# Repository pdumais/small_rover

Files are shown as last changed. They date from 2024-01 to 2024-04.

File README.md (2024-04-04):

# A remote controlled vehicle with a mechanical arm using ESP32 and a PS5 Dualsense controller
It's heavy, it's noisy, it's klonky and it looks like a rudimentary machine. That's exactly what I wanted to build.
This is work in progress, so no pictures of the final build yet

Rover (https://youtu.be/MDsiWHeAhvQ)
Rover (https://youtu.be/R3Qs6OE4Az8)

# Electronics
I chose to use 2 ESP32. It would have been easier to use just one, but I needed the memory of a esp32-s3 and the classic BT from the ESP32. So I'm using both. 
The ESP32 is the DualSense (PS5 controller) receiver. It handles the connection and incoming data from the Dualsense
and sends it on the i2c bus. This device will most probably end up handling other misc stuff too.

The esp32-s3 is main controller.
    - Controls the 4 motors
    - Controls servo for steering
    - Reads pulse count for each motors (RPM reading)
    - Controls the buzzer
    - Controls LED ring
  
# Choice of motors
I'm using 4 12v DC motors with a stall current of 7A with 4 DRV8871 that limits current to 2A for each motor.
The PWM signal to control the motor is shared for all DRV8871 so 4WD is disabled by software. Emiting the PWM on 3 more pins 
and requiring the motors would enable 4WD.

I tried to do the maths for calculating how big of a motor I would need to make something from steel, so targeting 5kgs.
Every number I came with gave me way too big requirements for motor size. This didn't make any sense considering the current offer of motors. So I decided to aim 251RPM and get high torque. 50$ a motor sounded like expensive so I guess it's good.
It turns out the torque is sufficient since the drv8871 doesn't seem to suffer. But 251RPM is faster than what I need. I would half that if I have to buy new motors.

After shopping around, it seems like building something that requires more than 10A of total current draw would be a different game. Different manufacturer and different tutorials. This hinted me that I should stick to this limit.

# PS5 Controller
I found an ESP32 ps5 library at https://github.com/rodneybakiskan/ps5-esp32.git but it was made for Arduino and is not maintained.
So I modified it to make it work outside the Arduino environment with only ESP-IDF. I'm having problems with it though. 
Connecting the controller is a hit or miss, sometimes I have to reboot the board and retry many times. But it works fine when 
using the Arduino version. I suspect it has something to do with multithreading/multicore since there seems to be a race condition when the controller tries to connect to the board and the board tries to connect to the controller at the same time. So I disabled the connection attempt from the board and it now works. I'll have to make a better fix later.

The controller is a bluetooth device so it has a range limit of 10m, but that's not an issue since I only plan on using this in the house.

# Frame
I chose to use steel for the frame. Aluminum would be better, but I don't have the tools to work aluminum. Plus, aluminum is expensive.
I developed an interest in welding lately so I wanted to play around with my tools.

## Motor mounts
The motor mounting brackets were a bit of a challenge for me. I used a piece of paper and poke holes where the screw holes of them motor were. Then I glued the the paper on a sheet of metal and cut/drilled it.

Of course the first piece I built was bad, but the second one only has 1 hole misaligned. Close enough.
So I now use that piece as a template to build more.

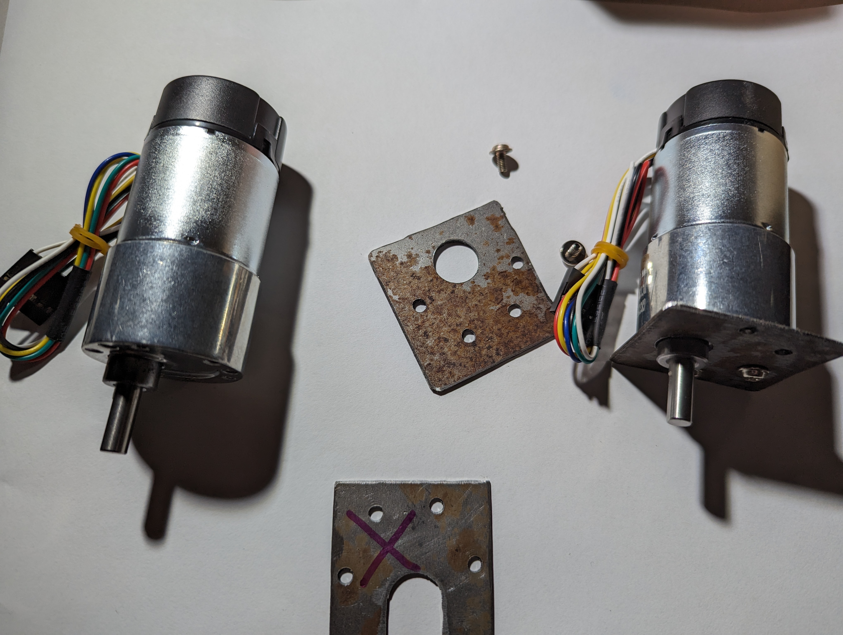
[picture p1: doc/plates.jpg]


## Subframe
The subframe is just a 3cm wide steel bar welded on the rear axle and bolted on the from one. I prefered to put bolts on the front s o it would be easier to put a better steering mechanism in place some time.

The vehicle is separated in 4 sections: The steering, battery mount, main board and mechanical arm.
There is a series of holes on the subframe that allows me to bolt the battery mount and main board at varying distances.

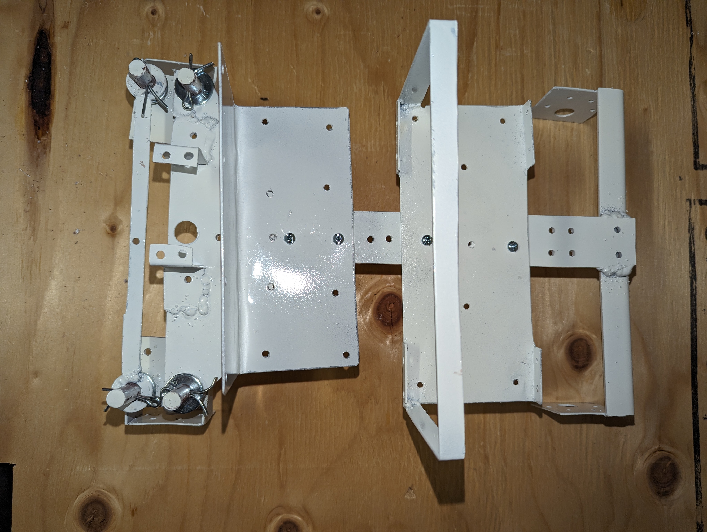
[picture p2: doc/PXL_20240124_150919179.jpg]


# Steering
To build a steering, I practiced a few prototypes with Legos. Then I ended up building something like this:
It's not perfect, but it works. Using ball joints would be much better.
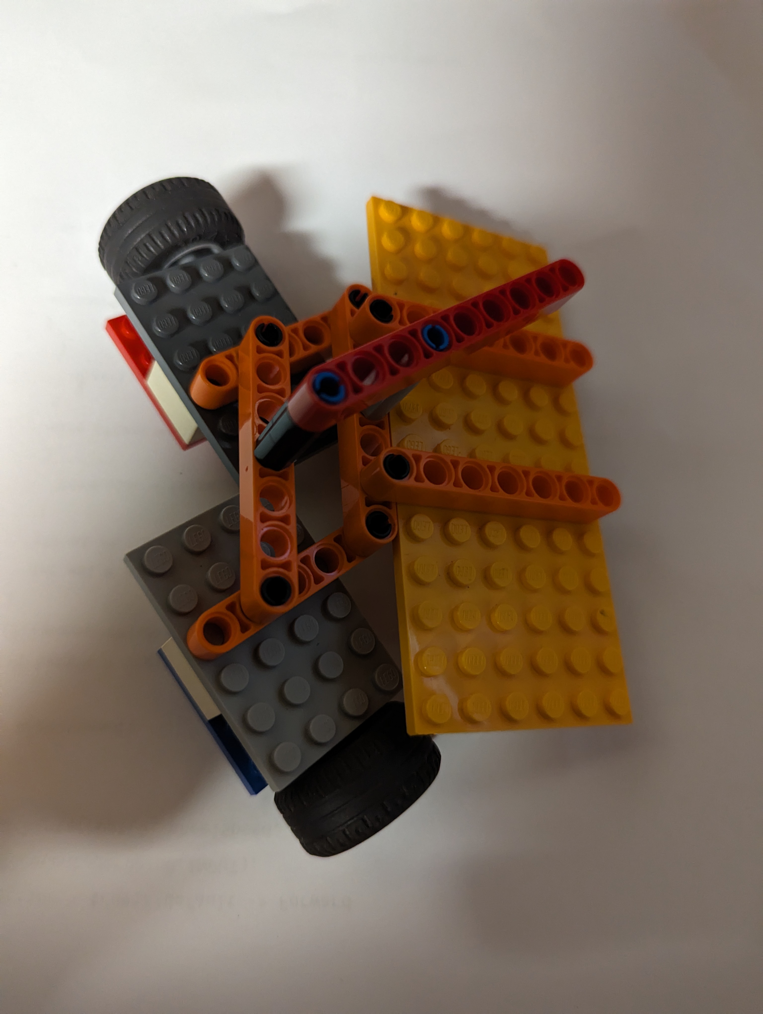
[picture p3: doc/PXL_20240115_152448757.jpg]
<p style="text-align: center;"> 
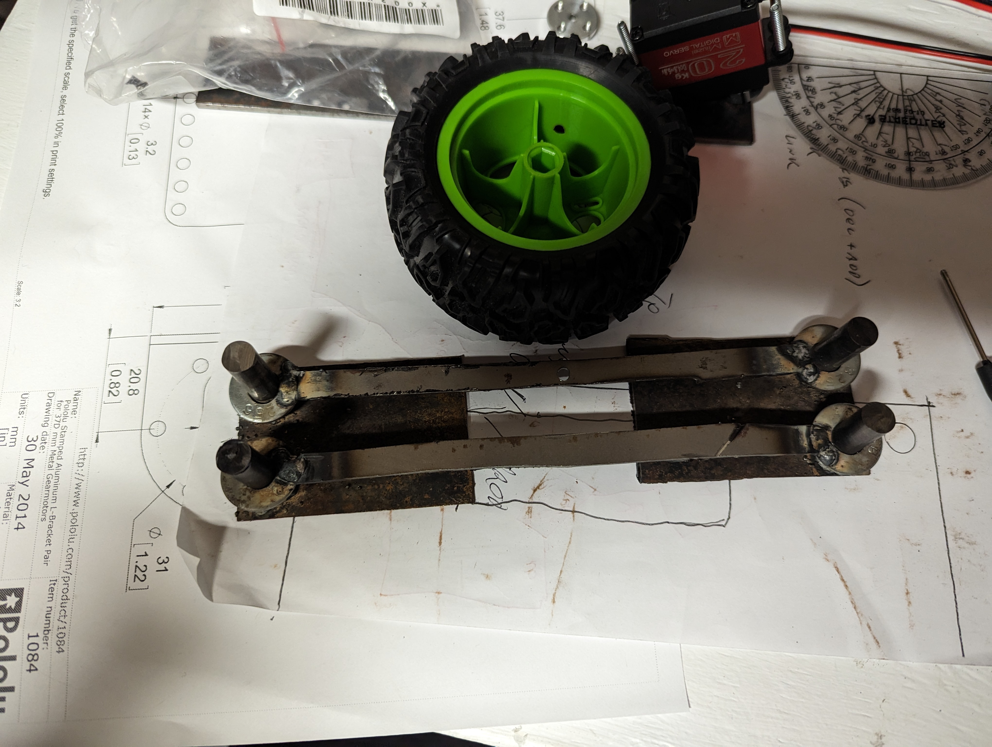
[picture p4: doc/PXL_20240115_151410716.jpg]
</p>

# Battery mount
The battery mount is just an L-shape plate on which the battery is tie-wrapped.
The battery sits on a foam to reduce vibrations.

# Main board
The main board is a piece of plywood on which all PCBs are screwed. It consists of the main ESP32 board, the PS5 controller ESP32 board and 2 small 5v regulators.

** Update march 1st.
I created a PCB design to make things a bit more cleaner. I dit not receive the board from the fab yet, but I'm planning on replacing the protoboard with this one

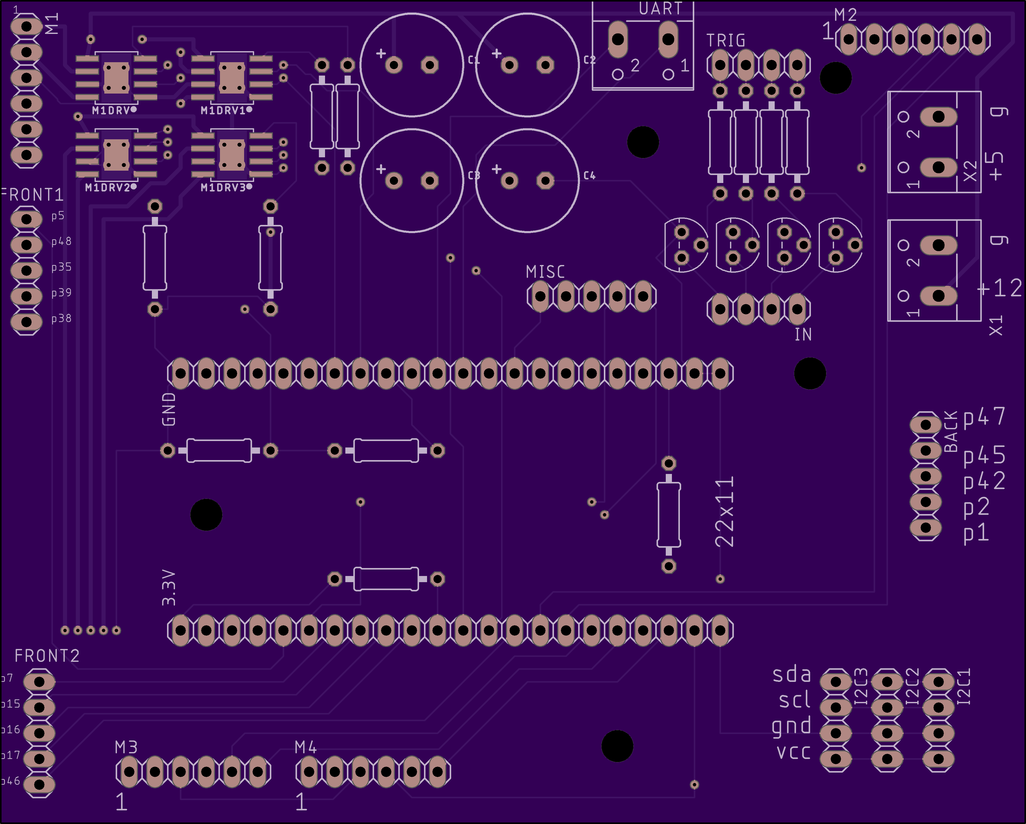
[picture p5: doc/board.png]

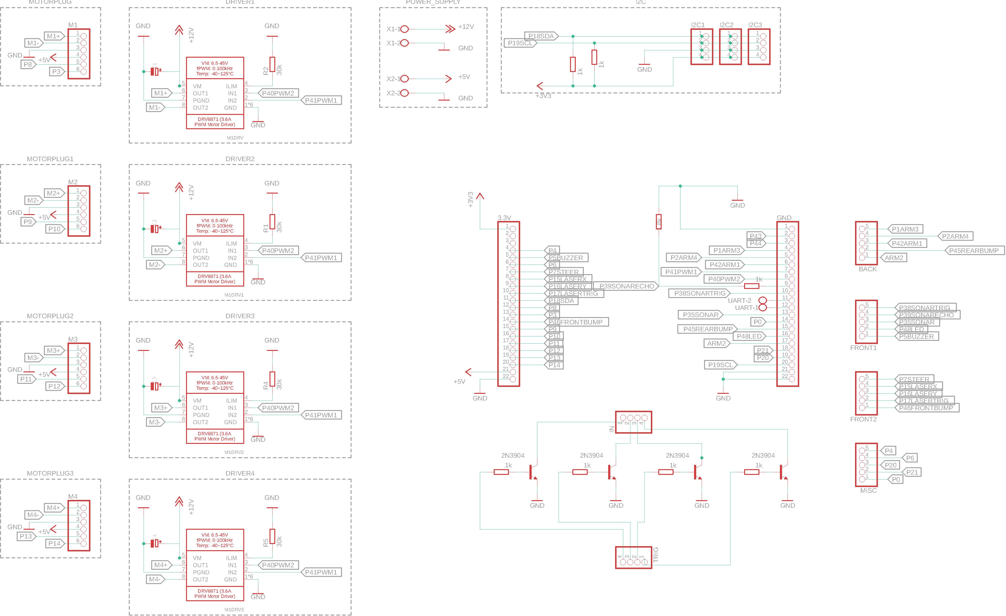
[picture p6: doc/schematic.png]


** Update April 2nd.

I finally got the board mounted on the robot.  As with all boards I make, there are a few design flaws on this one. But nothing that can't be fixed. The first issue is that I didn't think about the fact the motors on the right side would need to turn the opposite way from the ones on the left side. So I should've reverse the ouput lines comming from the motor driver for those. The fix was to simply reverse the pins on the motor connectors.

The 2nd flaw is that the 3 signal lines going to the servos for the laser and the sonar are running right above the motor output lines. So when I start the motors, it creates noise on the signal lines and the servos are going crazy. The fix for this was to add a 1k resistor inline on the signal cables. I'm not sure if that's the right fix, but it does work. It's nice to see how the noise being introduced is proportional to the current being used by the motors. For example, noise only happens what starting the motors or stopping them. I understand how electromagnectic induction works, but I didn't think it would be this sensitive.
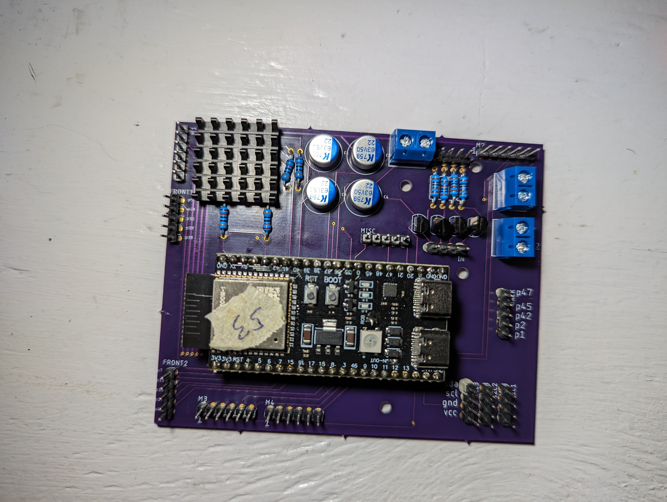
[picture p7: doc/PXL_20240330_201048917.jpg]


# Mechanical Arm
The goal was to be able to lift a 500ml can of beer.

- Base
    - Sits on bearing. Base is a big gear but not 360. Like the chute of a snoblower
    - regular DC motor with gear to spin the base. 
        - No need for high torque. No need for high speed although the gear ratio of the base must be taken in consideration

- Boom and Arm
    - 2 regular motors. Or servos? Servos cant be controlled like a real bakhoe
    - Sitting on the base. Pulling the boom and arm using levers
- Grapple
    - Servo sitting on the arm

I wanted the feel of the arm to be like a backhoe control. My initial implementation was taking a value from the Dualsense constroller sticks. This value is between -128 and 127 and was mapped to an angle on the betwwen 0 and 90 on the servo.
This has the affect of using the controller to bring the arm to a set value instead of simply accellerating the arm, like a hydraulic system would. This is a big difference in feel. Also, when releasing the DualSense stick, the servo would return back to its original position. In a hydraulic system, you simply want the arm to stop moving and stay at its current position.

It took a fair amount of code to replicate this behaviour but I'm overall satisfied. It definitely feels more "mechanic" that fluid like a hydraulic system but I think I like it.

The arm can only be used while in "arm" mode. Arm mode is activated/deactivated with the Dualsense cross button.
While in arm mode, the throttle is disabled and the steering is disable to be able to use the sticks for controlling the arm.
Another reason, is that it would require too much power to run the 4 motors and the servos at the same time.
To reduce power usage event more, only 1 servo per sticks can be used at the same time. The 5v regulator that feeds the servo cannot exceed 3A.

# Telemetry
The machine creates a WAP and has the IP address 192.168.4.1. It sends telemetry data over a websocket every second. This packet
contains the metrics of the machine as defined in [mainboard/main/common.h](mainboard//main/common.h) in `struct metrics_t`. There is web page served on port 80 to render the raw data into a user friendly view.
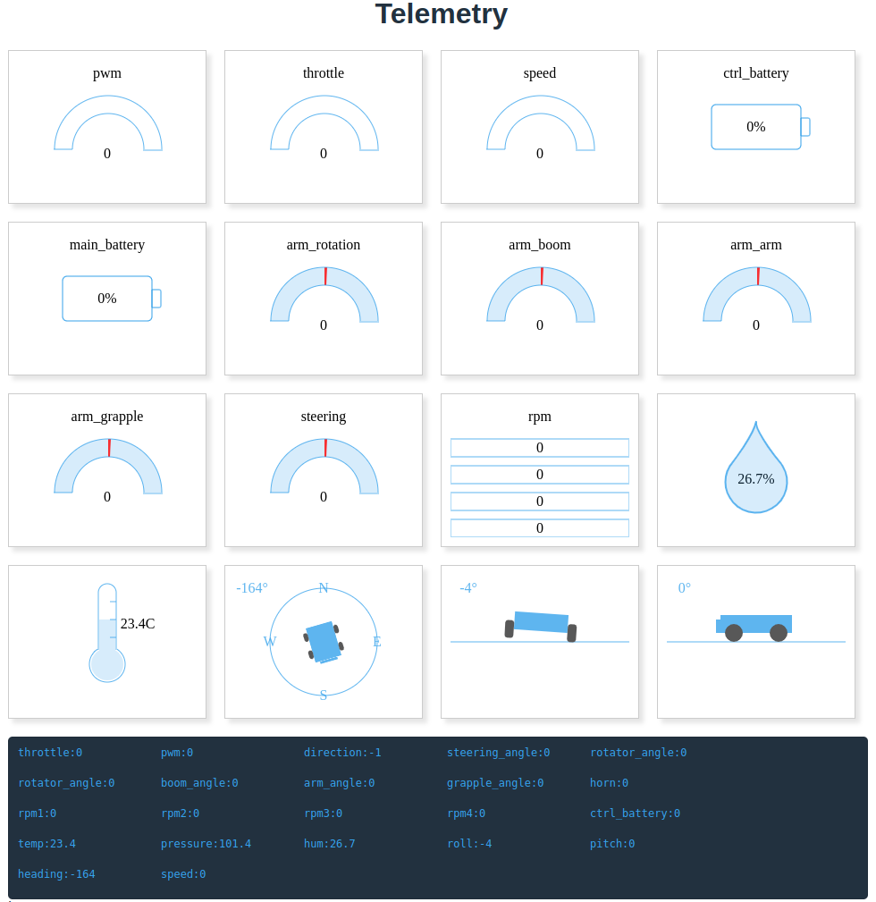
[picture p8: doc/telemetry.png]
<p style="text-align: center;"> 

# Wifi
The vehicle creates a WAP called "ROVER". I've configured my router to auto-connect to that WAP and take the address 192.168.4.2.
The router then forwards UDP 242 to my dev machine so I can receive stats broadcast while developing.

From my dev machine, I can also trigger a OTA firmware upgrade so I don't need to connect the vehicle with a USB cable anymore.

# Recording
The vehicle can learn routes by recording user inputs while controlling with the dualsense.
The Circle button enters the machine into recording mode. It starts recording all throttle changes and steering angle changes as the user operates the machine. Pressing the triangle button replays a recording. 

By replaying the same throttle values and steering angle at the same time deltas, the machine should be able to replicate the same path that was recorded but it needs to be placed at the same starting position than the recording was made at.

I was initially thinking of using a digital magnetometer but I don't think it would give me
much more precision than what I currently get. A GPS would be great, but won't work indoor and the accuracy would be lower (1.5m margin of error I believe).

In practice, the replay is not 100% accurate because I suspect that the tires slip on the floor in a different way each time. There is also a margin of error in the timing. The results are quite good still, but the machine doesn't come back exactly where it was all the time, but quite close.

Rover (https://www.youtube.com/watch?v=QwFZJzM8oCE)

The record buffer is a bit small too. It can hold up to 300 events and then recording stops. I am planning on flushing the buffer to flash when it is full and be able to record at least 1000 events.

# Improvements
There are many design flaws with this machine. Mostly because of my limited knowledge about mechanics and electronics, but also because
of a consious choice to sacrifice performance to be able to use limited resources. For example, a few pivot points would gain by being installed on a bearing or ball joint, but this would have become too expensive. I had everything on hand already to build a poorman's version. I like to think of it as working as if in a post-apocalyptic world and scavanging for parts :)

# Pictures

Project status Jan 17
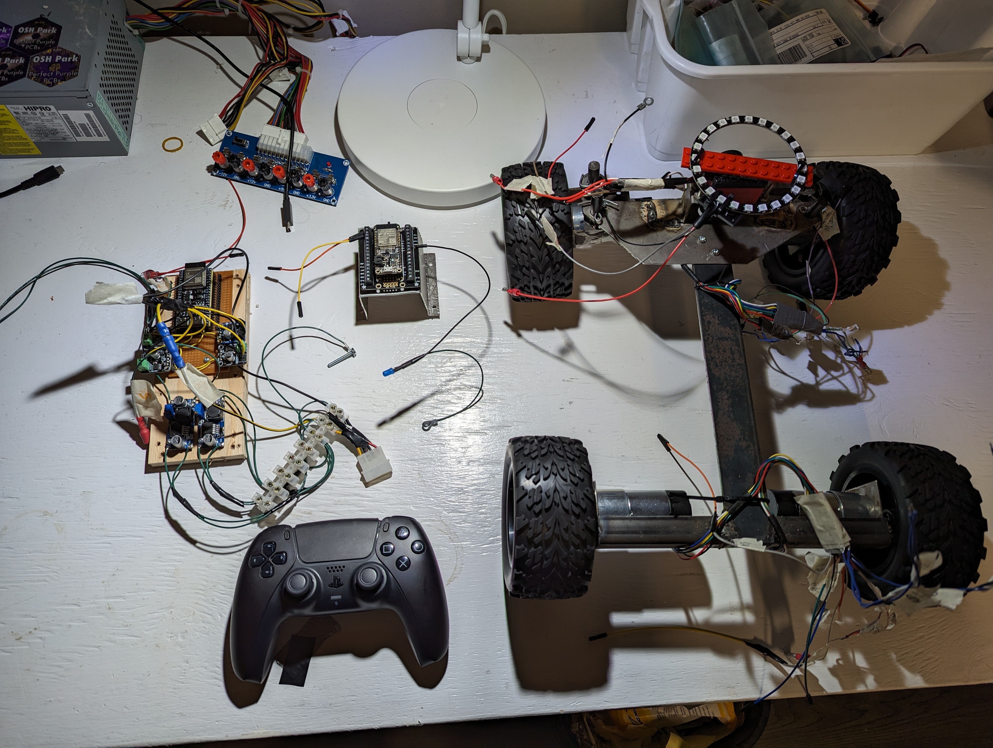
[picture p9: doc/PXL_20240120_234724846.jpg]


Guts and wheels mounted
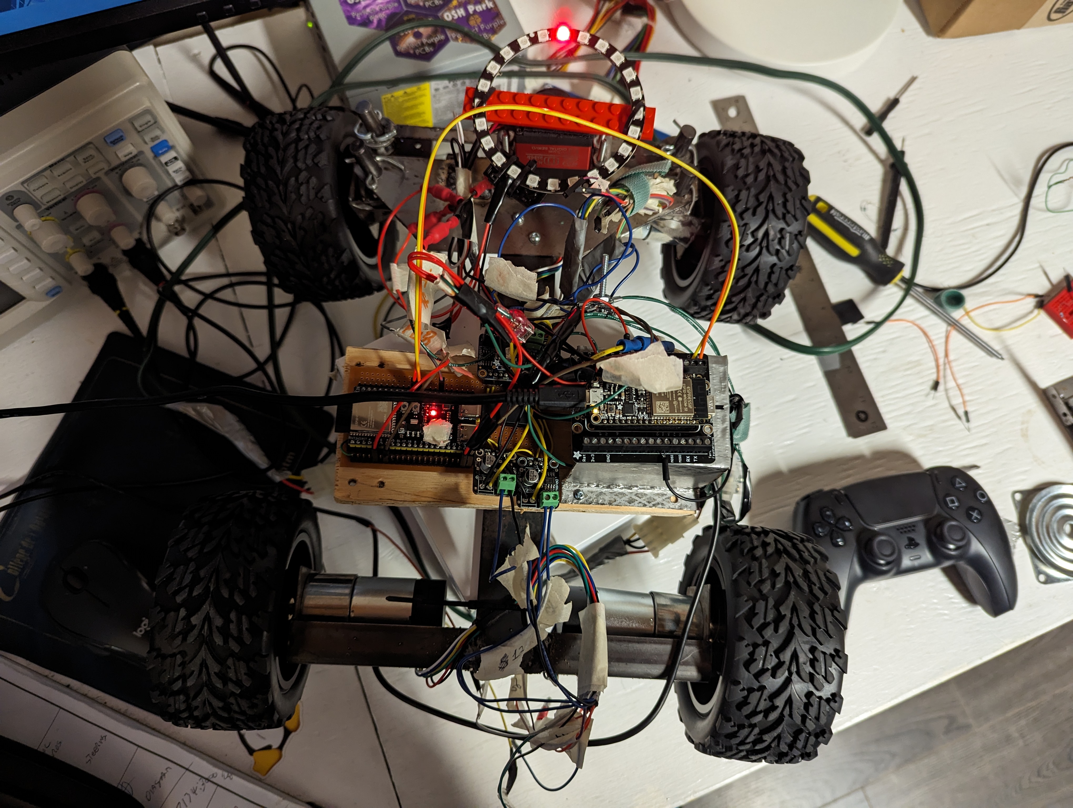
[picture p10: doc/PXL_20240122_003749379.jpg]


Project status Jan 22
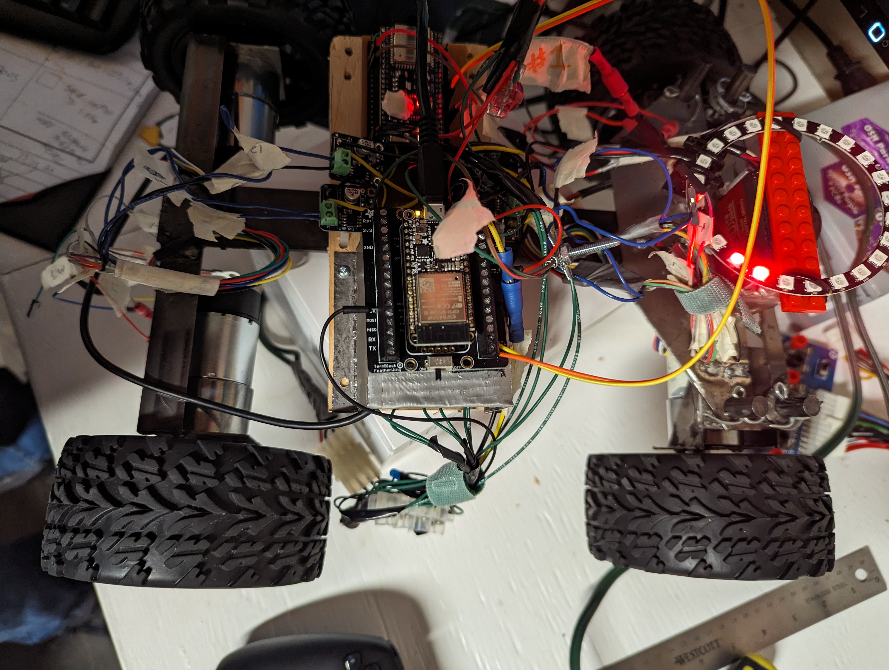
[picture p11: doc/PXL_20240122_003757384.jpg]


Prototype is working. I'm ready to finish the frame. So it's now time to disassemble everything.
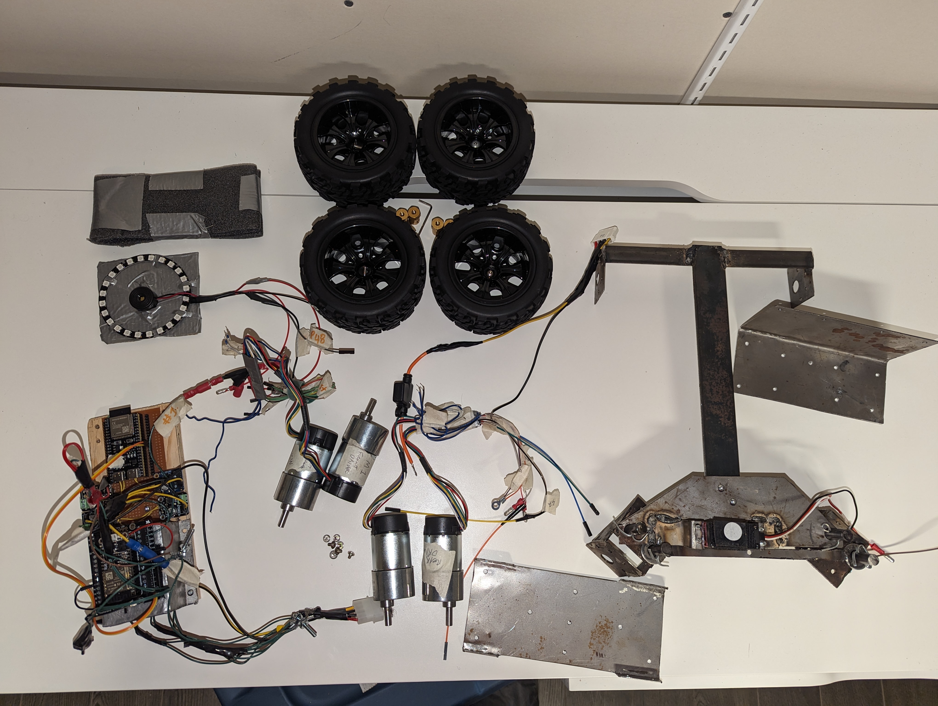
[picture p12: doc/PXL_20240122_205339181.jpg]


Everything is painted. I just need to let it dry 24h and I will re-assemble everything
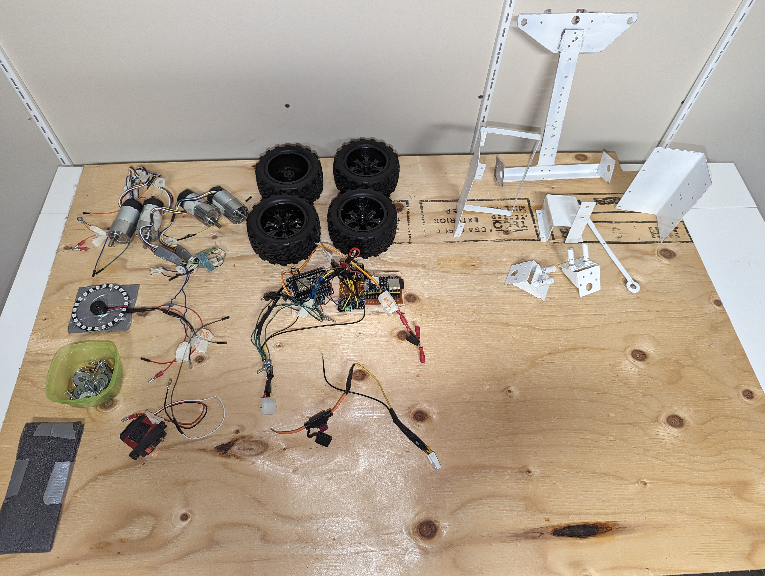
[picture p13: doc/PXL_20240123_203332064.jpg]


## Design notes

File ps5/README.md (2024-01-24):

This is adapted from https://github.com/rodneybakiskan/ps5-esp32. The library was modified to work outside of Arduino and also has a few bug fixes.

The PS5 controller code runs on a ESP32. It cannot run on esp32s3 since that device only supports BLE.
This software listens for incoming dualsense events and forwards them on the i2c bus.

# Building
Everything runs in docker, no need to install ESP IDF

- Change the dualsense MAC address in app_main.c
- run ./build.sh
- change the USB port to target your esp32 device in flash.sh
- run ./flash.sh

# Pairing
On the first usage, the dualsense needs to be put in pairing mode. Then the pairing will be done automatically.

# Known issues
There is sometimes a crash:
    E (30465) BT_L2CAP: L2CAP got conn_comp in bad state: 4  status: 0x4
    I (30465) ps5_L2CAP: [ps5_l2cap_disconnect_ind_cback] l2cap_cid: 0x41 ack_needed: 0
    I (30475) ps5_L2CAP: [ps5_l2cap_disconnect_ind_cback] l2cap_cid: 0x42 ack_needed: 0
    I (30475) ps5_L2CAP: [ps5_l2cap_disconnect_ind_cback] l2cap_cid: 0x40 ack_needed: 0
    W (30485) BT_HCI: hcif conn complete: hdl 0xfff, st 0x4
    E (30495) BT_L2CAP: L2CAP - rcvd ACL for unknown handle:128 ls:0 cid:64 opcode:161 cur count:0

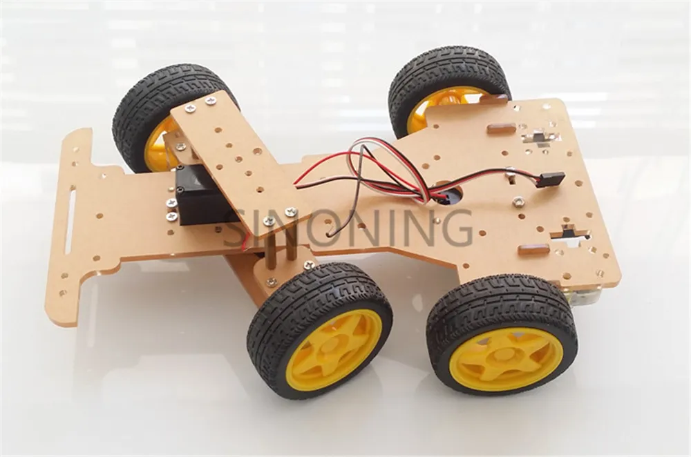
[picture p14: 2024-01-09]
doc/steering.webp

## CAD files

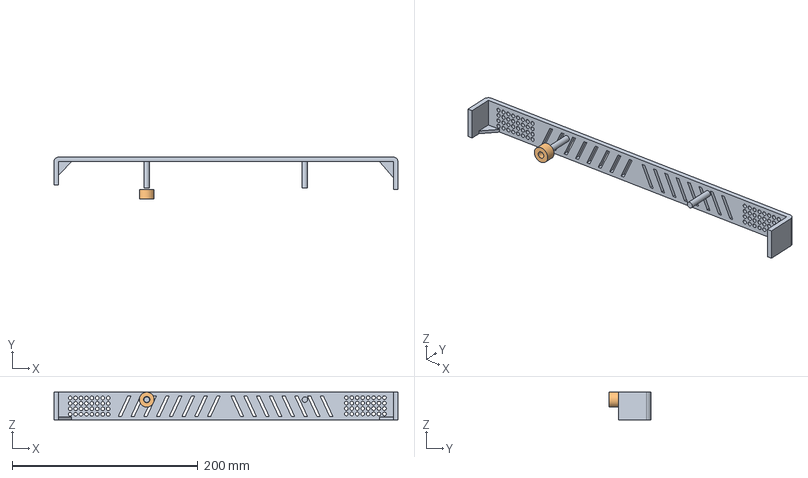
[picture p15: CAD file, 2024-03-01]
cad/bumper-rear.FCStd
370.0 x 45.0 x 30.0 mm

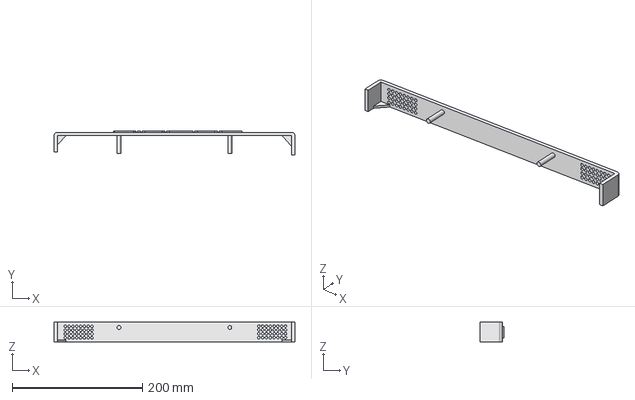
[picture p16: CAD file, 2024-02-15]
cad/bumper.FCStd
370.0 x 37.0 x 30.0 mm

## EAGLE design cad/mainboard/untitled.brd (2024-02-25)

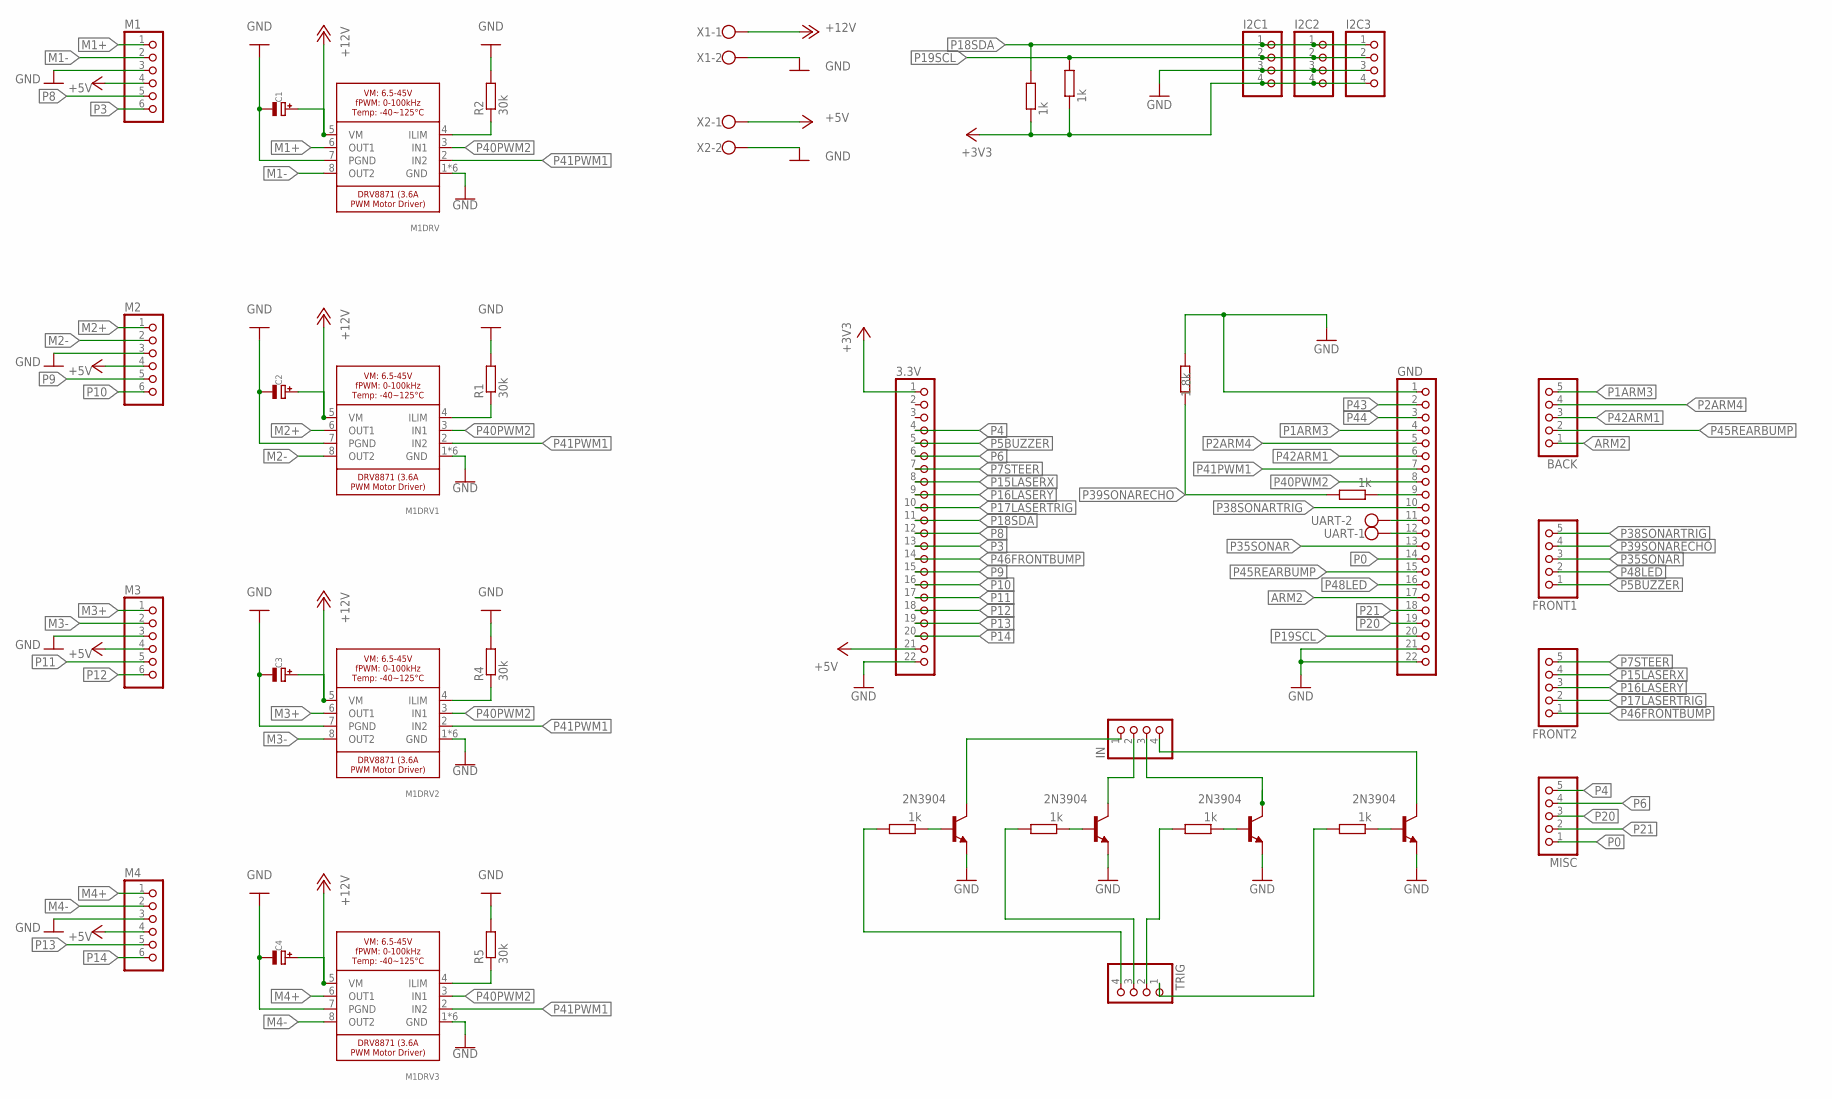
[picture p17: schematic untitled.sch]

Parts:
1K, 1K1, 1K3, 1K4, 1K5, 1K6: 1k; 0207/10
1K2: 1.8k; 0207/10
3.3V: PINHD-1X22; 1X22
BACK: PINHD-1X5; 1X05
C1, C2, C3, C4: MICROBUILDER_CAP_ELECTROLYTICPTH_3.5MMGRID_10MMDIA; MICROBUILDER_CELEC_3.5MM_10MM
FRONT1, FRONT2: PINHD-1X5; 1X05
GND: PINHD-1X22; 1X22
I2C1, I2C2, I2C3: PINHD-1X4; 1X04
IN: PINHD-1X4; 1X04
M1, M2, M3, M4: PINHD-1X6; 1X06
M1DRV, M1DRV1, M1DRV2, M1DRV3: MICROBUILDER_DRV8871; MICROBUILDER_HSOP8
MISC: PINHD-1X5; 1X05
R1, R2, R4, R5: 30k; 0207/10
R3: 1k; 0207/10
T1, T2, T3, T4: 2N3904; TO92
TRIG: PINHD-1X4; 1X04
UART: W237-102
X1, X2: W237-102

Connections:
+3V3: 1K.1, 3.3V.1, I2C1.4, I2C2.4, I2C3.4, R3.1
+5V: 3.3V.21, M1.4, M2.4, M3.4, M4.4, X2.1
+12V: C1.+, C2.+, C3.+, C4.+, M1DRV.5 (VM), M1DRV1.5 (VM), M1DRV2.5 (VM), M1DRV3.5 (VM), X1.1
ARM2: BACK.1, GND.17
GND: 1K2.1, 3.3V.22, C1.-, C2.-, C3.-, C4.-, GND.1, GND.21, GND.22, I2C1.3, I2C2.3, I2C3.3, M1.3, M1DRV.1 (GND), M1DRV.7 (PGND), M1DRV.GND, M1DRV.P$1 (GND), M1DRV.P$2 (GND), M1DRV.P$3 (GND), M1DRV.P$4 (GND), M1DRV1.1 (GND), M1DRV1.7 (PGND), M1DRV1.GND, M1DRV1.P$1 (GND), M1DRV1.P$2 (GND), M1DRV1.P$3 (GND), M1DRV1.P$4 (GND), M1DRV2.1 (GND), M1DRV2.7 (PGND), M1DRV2.GND, M1DRV2.P$1 (GND), M1DRV2.P$2 (GND), M1DRV2.P$3 (GND), M1DRV2.P$4 (GND), M1DRV3.1 (GND), M1DRV3.7 (PGND), M1DRV3.GND, M1DRV3.P$1 (GND), M1DRV3.P$2 (GND), M1DRV3.P$3 (GND), M1DRV3.P$4 (GND), M2.3, M3.3, M4.3, R1.2, R2.2, R4.2, R5.2, T1.3 (E), T2.3 (E), T3.3 (E), T4.3 (E), X1.2, X2.2
IN: IN.1, T4.1 (C)
M1+: M1.1, M1DRV.6 (OUT1)
M1-: M1.2, M1DRV.8 (OUT2)
M2+: M1DRV1.6 (OUT1), M2.1
M2-: M1DRV1.8 (OUT2), M2.2
M3+: M1DRV2.6 (OUT1), M3.1
M3-: M1DRV2.8 (OUT2), M3.2
M4+: M1DRV3.6 (OUT1), M4.1
M4-: M1DRV3.8 (OUT2), M4.2
unnamed: M1DRV1.4 (ILIM), R1.1
unnamed: M1DRV2.4 (ILIM), R4.1
unnamed: 1K1.1, GND.9
unnamed: M1DRV3.4 (ILIM), R5.1
unnamed: GND.11, UART.2
unnamed: GND.12, UART.1
unnamed: IN.2, T1.1 (C)
unnamed: 1K3.1, T1.2 (B)
unnamed: M1DRV.4 (ILIM), R2.1
unnamed: 1K3.2, TRIG.3
unnamed: IN.3, T2.1 (C)
unnamed: 1K4.1, T2.2 (B)
unnamed: 1K4.2, TRIG.2
unnamed: IN.4, T3.1 (C)
unnamed: 1K5.1, T3.2 (B)
unnamed: 1K5.2, TRIG.1
unnamed: 1K6.1, T4.2 (B)
unnamed: 1K6.2, TRIG.4
P0: GND.14, MISC.1
P1ARM3: BACK.5, GND.4
P2ARM4: BACK.4, GND.5
P3: 3.3V.13, M1.6
P4: 3.3V.4, MISC.5
P5BUZZER: 3.3V.5, FRONT1.1
P6: 3.3V.6, MISC.4
P7STEER: 3.3V.7, FRONT2.5
P8: 3.3V.12, M1.5
P9: 3.3V.15, M2.5
P10: 3.3V.16, M2.6
P11: 3.3V.17, M3.5
P12: 3.3V.18, M3.6
P13: 3.3V.19, M4.5
P14: 3.3V.20, M4.6
P15LASERX: 3.3V.8, FRONT2.4
P16LASERY: 3.3V.9, FRONT2.3
P17LASERTRIG: 3.3V.10, FRONT2.2
P18SDA: 1K.2, 3.3V.11, I2C1.1, I2C2.1, I2C3.1
P19SCL: GND.20, I2C1.2, I2C2.2, I2C3.2, R3.2
P20: GND.19, MISC.3
P21: GND.18, MISC.2
P35SONAR: FRONT1.3, GND.13
P38SONARTRIG: FRONT1.5, GND.10
P39SONARECHO: 1K1.2, 1K2.2, FRONT1.4
P40PWM2: GND.8, M1DRV.3 (IN1), M1DRV1.3 (IN1), M1DRV2.3 (IN1), M1DRV3.3 (IN1)
P41PWM1: GND.7, M1DRV.2 (IN2), M1DRV1.2 (IN2), M1DRV2.2 (IN2), M1DRV3.2 (IN2)
P42ARM1: BACK.3, GND.6
P43: GND.2
P44: GND.3
P45REARBUMP: BACK.2, GND.15
P46FRONTBUMP: 3.3V.14, FRONT2.1
P48LED: FRONT1.2, GND.16

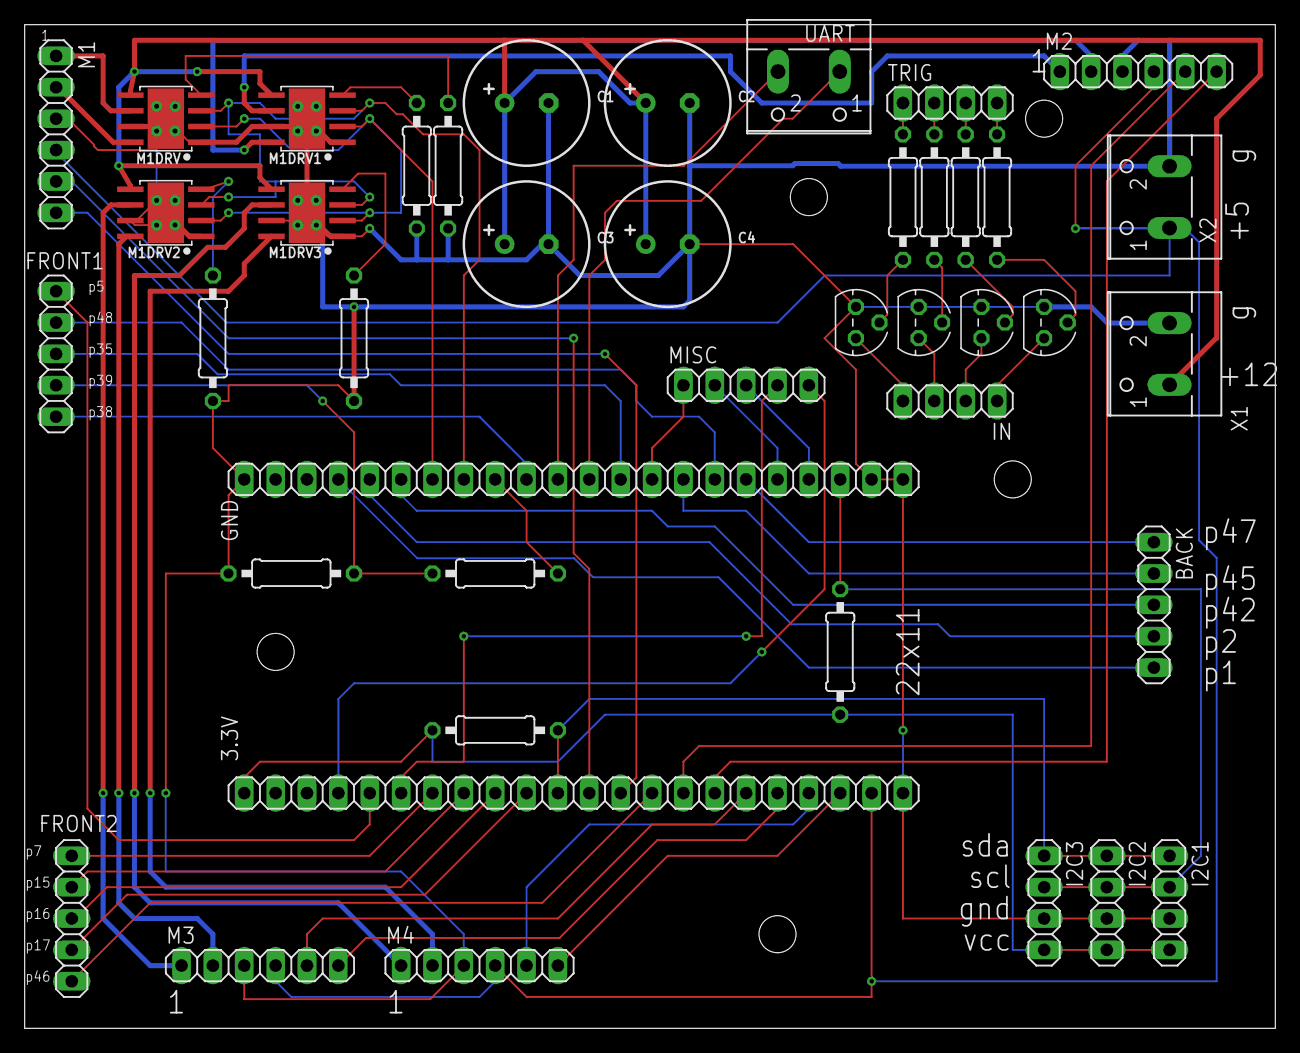
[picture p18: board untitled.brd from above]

Board: 2 copper layers, 101.3 x 81.3 mm, 42 parts (0 on the bottom side), 63 nets.

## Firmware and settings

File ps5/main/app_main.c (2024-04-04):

#include <stdio.h>
#include <string.h>

#include <freertos/FreeRTOS.h>
#include <freertos/task.h>
#include <freertos/event_groups.h>
#include <esp_wifi.h>
#include <esp_system.h>
#include <esp_log.h>
#include <esp_event.h>
#include <nvs_flash.h>
#include "driver/uart.h"
#include "driver/gpio.h"
#include "ps5_controller.h"
#include "common/i2c.h"
#include "common/deepsleep.h"
#include <esp_timer.h>
#include "esp_adc/adc_oneshot.h"

#define DUALSENSE_MAC "D0:BC:C1:EC:AD:AC"
#define GPIO_CTRL_LED 5
#define GPIO_PAIR 18
#define GPIO_SLEEP_BUTTON GPIO_NUM_4
#define ADC_RESULT_SIZE 256
#define UART_TX_PIN 22
#define UART_RX_PIN 23
#define ADC_READ_LEN 256

static const char *TAG = "ps5_main";
static volatile ps5_t old_data = {0};
static QueueHandle_t uart_queue;
static adc_oneshot_unit_handle_t adc_battery_handle;

void init_nvs()
{
    /* Initialize NVS partition */
    esp_err_t ret = nvs_flash_init();
    if (ret == ESP_ERR_NVS_NO_FREE_PAGES || ret == ESP_ERR_NVS_NEW_VERSION_FOUND)
    {
        /* NVS partition was truncated
         * and needs to be erased */
        ESP_ERROR_CHECK(nvs_flash_erase());

        /* Retry nvs_flash_init */
        ESP_ERROR_CHECK(nvs_flash_init());
    }
}

static void uart_init(void)
{
    ESP_LOGI(TAG, "uart_init");

    ESP_ERROR_CHECK(uart_driver_install(UART_NUM_2, 1024, 0, 0, 0, 0));

    uart_config_t uart_config = {
        .baud_rate = 115200,
        .data_bits = UART_DATA_8_BITS,
        .parity = UART_PARITY_DISABLE,
        .stop_bits = UART_STOP_BITS_1,
        .flow_ctrl = UART_HW_FLOWCTRL_DISABLE};
    ESP_ERROR_CHECK(uart_param_config(UART_NUM_2, &uart_config));
    ESP_ERROR_CHECK(uart_set_pin(UART_NUM_2, UART_TX_PIN, UART_RX_PIN, -1, -1));
}

void set_checksum(ps5_t *data)
{
    data->checksum = 0;
    uint8_t c = 0;
    for (int i = 0; i < sizeof(ps5_t) - 1; i++)
    {
        c += ((uint8_t *)data)[i];
    }
    data->checksum = c;
}

void rumble(bool state)
{
    if (state)
    {
        ps5_set_rumble(255, 255);
    }
    else
    {
        ps5_set_rumble(0, 0);
    }
}

void set_pad_led(uint8_t r, uint8_t g, uint8_t b)
{
    ps5_set_led(r, g, b);
}

static unsigned long millis()
{
    return (unsigned long)(esp_timer_get_time() / 1000ULL);
}

void ps5_check(void *arg)
{
    bool was_connected = 0;
    esp_err_t err;
    unsigned long current_millis = millis();
    unsigned long turn_off_rumble_millis = 0;
    int adc_result;
    int adc_val = 0;
    int average_count = 20;

    int battery_mv = 0;
    while (1)
    {
        current_millis = millis();
        if (turn_off_rumble_millis != 0 && turn_off_rumble_millis < current_millis)
        {
            ESP_LOGI(TAG, "UNSET RUMBLE %lu %lu", current_millis, turn_off_rumble_millis);
            ps5_set_rumble(0, 0);
            turn_off_rumble_millis = 0;
        }

        if (!ps5_isConnected())
        {
            if (was_connected)
            {
                ESP_LOGI(TAG, "Controller disconnected");
                was_connected = false;
                ps5_t *data = ps5_get_data();
                data->controller_connected = 0;
                data->latestPacket = 1;
                set_checksum(data);
                uart_write_bytes(UART_NUM_2, data, sizeof(ps5_t));
            }

            gpio_set_level(GPIO_CTRL_LED, 0);
            ESP_LOGI(TAG, "Not connected to PS5 controller");
            vTaskDelay(3000 / portTICK_PERIOD_MS);
            continue;
        }

        // At this point, we know the ps5 controller is connected
        if (!was_connected)
        {
            ESP_LOGI(TAG, "Controller Connected");
            was_connected = false;
            ps5_t *data = ps5_get_data();
            data->controller_connected = 1;
            data->latestPacket = 1;
            set_checksum(data);
            uart_write_bytes(UART_NUM_2, data, sizeof(ps5_t));

            was_connected = 1;
        }

        gpio_set_level(GPIO_CTRL_LED, 1);
        ps5_t *data = ps5_get_data();

        bool has_changes = (data->button.right != old_data.button.right ||
                            data->button.left != old_data.button.left ||
                            data->button.up != old_data.button.up ||
                            data->button.down != old_data.button.down ||
                            data->button.square != old_data.button.square ||
                            data->button.circle != old_data.button.circle ||
                            data->button.cross != old_data.button.cross ||
                            data->button.triangle != old_data.button.triangle ||
                            data->button.l1 != old_data.button.l1 ||
                            data->button.r1 != old_data.button.r1 ||
                            data->button.l2 != old_data.button.l2 ||
                            data->button.r2 != old_data.button.r2 ||
                            data->button.l3 != old_data.button.l3 ||
                            data->button.r3 != old_data.button.r3 ||
                            abs(data->analog.stick.lx - old_data.analog.stick.lx) > 2 ||
                            abs(data->analog.stick.ly - old_data.analog.stick.ly) > 2 ||
                            abs(data->analog.stick.rx - old_data.analog.stick.rx) > 2 ||
                            abs(data->analog.stick.ry - old_data.analog.stick.ry) > 2 ||
                            abs(data->analog.button.l2 - old_data.analog.button.l2) > 2 ||
                            abs(data->analog.button.r2 - old_data.analog.button.r2) > 2);

        if (has_changes)
        {

            ESP_LOGI(TAG, "PS5 Event. throttle: %i", data->analog.button.r2);

            memcpy(&old_data, data, sizeof(ps5_t));
            old_data.latestPacket = true;
            old_data.controller_connected = true;
            old_data.main_battery = battery_mv;
            set_checksum(&old_data);

            uart_write_bytes(UART_NUM_2, &old_data, sizeof(ps5_t));
            // uart_wait_tx_done(UART_NUM_2
        }

        controller_message ctrl_msg = {0};
        size_t size = uart_read_bytes(UART_NUM_2, &ctrl_msg, sizeof(controller_message), 50 / portTICK_PERIOD_MS);

        if (ctrl_msg.command != 0)
        {
            if (ctrl_msg.command == 0x01)
            {
                ps5_set_led(ctrl_msg.data1, ctrl_msg.data2, ctrl_msg.data3);
            }
            else if (ctrl_msg.command == 0x02)
            {
                ps5_trigger_effect(ctrl_msg.data1, ctrl_msg.data2, ctrl_msg.data3);
            }
            else if (ctrl_msg.command == 0x03)
            {
                ps5_set_rumble(255, 255);
                turn_off_rumble_millis = millis() + ((unsigned long)ctrl_msg.data1 * 1000ULL);
                ESP_LOGI(TAG, "SET RUMBLE %lu %lu", current_millis, turn_off_rumble_millis);
            }
        }

        /*
            13.29v -> 3200 (70%)
            13.12v -> 3080
            13.09v -> 3070
            13.08V -> 3056
        */
        ESP_ERROR_CHECK(adc_oneshot_read(adc_battery_handle, ADC_CHANNEL_5, &adc_result));
        adc_val += ((adc_result * 3276) / 4096); // values chosen during calibration
        average_count--;
        if (average_count == 0)
        {
            battery_mv = adc_val / 20;
            average_count = 20;
            adc_val = 0;
        }
    }
}

void on_start_sleep()
{
    gpio_set_level(GPIO_CTRL_LED, 0);
    vTaskDelay(200 / portTICK_PERIOD_MS);
    gpio_set_level(GPIO_CTRL_LED, 1);
    vTaskDelay(500 / portTICK_PERIOD_MS);
    gpio_set_level(GPIO_CTRL_LED, 0);
    vTaskDelay(200 / portTICK_PERIOD_MS);
    gpio_set_level(GPIO_CTRL_LED, 1);
    vTaskDelay(500 / portTICK_PERIOD_MS);
    gpio_set_level(GPIO_CTRL_LED, 0);
    vTaskDelay(200 / portTICK_PERIOD_MS);
    gpio_set_level(GPIO_CTRL_LED, 1);
    vTaskDelay(500 / portTICK_PERIOD_MS);
    gpio_set_level(GPIO_CTRL_LED, 0);
    vTaskDelay(200 / portTICK_PERIOD_MS);
    gpio_set_level(GPIO_CTRL_LED, 1);
    vTaskDelay(500 / portTICK_PERIOD_MS);
    gpio_set_level(GPIO_CTRL_LED, 0);
}

/*static bool IRAM_ATTR s_conv_done_cb(adc_continuous_handle_t handle, const adc_continuous_evt_data_t *edata, void *user_data)
{
    BaseType_t mustYield = pdFALSE;
    // Notify that ADC continuous driver has done enough number of conversions
    // vTaskNotifyGiveFromISR(s_task_handle, &mustYield);

    return (mustYield == pdTRUE);
}*/

void app_main(void)
{
    init_nvs();

    init_deep_sleep(GPIO_SLEEP_BUTTON, on_start_sleep);

    gpio_config_t i_conf = {};
    i_conf.pin_bit_mask = 0;
    i_conf.pin_bit_mask |= (1ULL << GPIO_PAIR);
    i_conf.intr_type = GPIO_INTR_DISABLE;
    i_conf.mode = GPIO_MODE_INPUT;
    i_conf.pull_up_en = 0;
    i_conf.pull_down_en = 1;
    gpio_config(&i_conf);

    gpio_config_t o_conf = {};
    o_conf.pin_bit_mask |= (1ULL << GPIO_CTRL_LED);
    o_conf.intr_type = GPIO_INTR_DISABLE;
    o_conf.mode = GPIO_MODE_OUTPUT;
    o_conf.pull_up_en = 1;
    o_conf.pull_down_en = 0;
    gpio_config(&o_conf);

    /*
    adc_continuous_handle_cfg_t adc_config = {
        .max_store_buf_size = 1024,
        .conv_frame_size = ADC_READ_LEN,
    };
    ESP_ERROR_CHECK(adc_continuous_new_handle(&adc_config, &adc_battery_handle));

    adc_continuous_config_t dig_cfg = {
        .sample_freq_hz = 20 * 1000,
        .conv_mode = ADC_CONV_SINGLE_UNIT_1,
        .format = ADC_DIGI_OUTPUT_FORMAT_TYPE1,
    };

    adc_digi_pattern_config_t adc_pattern[1] = {0};
    dig_cfg.pattern_num = 1;
    adc_pattern[0].atten = ADC_ATTEN_DB_12;
    adc_pattern[0].channel = ADC_CHANNEL_5 & 0x7;
    adc_pattern[0].unit = ADC_UNIT_1;
    adc_pattern[0].bit_width = ADC_BITWIDTH_12;
    dig_cfg.adc_pattern = adc_pattern;
    ESP_ERROR_CHECK(adc_continuous_config(adc_battery_handle, &dig_cfg));

    adc_continuous_evt_cbs_t cbs = {
        .on_conv_done = s_conv_done_cb,
    };
    ESP_ERROR_CHECK(adc_continuous_register_event_callbacks(adc_battery_handle, &cbs, NULL));
    ESP_ERROR_CHECK(adc_continuous_start(adc_battery_handle));
    */

    adc_oneshot_unit_init_cfg_t init_config1 = {
        .unit_id = ADC_UNIT_1,
    };
    ESP_ERROR_CHECK(adc_oneshot_new_unit(&init_config1, &adc_battery_handle));
    adc_oneshot_chan_cfg_t config = {
        .bitwidth = ADC_BITWIDTH_DEFAULT,
        .atten = ADC_ATTEN_DB_12,
    };
    ESP_ERROR_CHECK(adc_oneshot_config_channel(adc_battery_handle, ADC_CHANNEL_5, &config));

    uart_init();
    ps5_begin(DUALSENSE_MAC);
    /* Initialize the event loop */
    ESP_ERROR_CHECK(esp_event_loop_create_default());

    if (gpio_get_level(GPIO_PAIR) == 1)
    {
        ESP_LOGI(TAG, "Waiting to pair");
        ps5_try_pairing();
    }

    xTaskCreate(ps5_check, "ps5_check", 4096, NULL, 5, NULL);
}

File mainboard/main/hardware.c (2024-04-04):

#include "driver/gpio.h"
#include <esp_system.h>
#include <esp_event.h>
#include <nvs_flash.h>
#include <esp_log.h>
#include <esp_event_base.h>
#include "hardware.h"
#include "common.h"
#include "driver/pcnt.h"
#include "led_sequence.h"
#include "common/ps5_data.h"
#include "common/i2c.h"
#include "common/deepsleep.h"
#include "hw_def.h"
#include "wifi.h"
#include "led.h"
#include "buzzer.h"
#include <memory.h>
#include "servo.h"
#include "arm.h"
#include "routerecorder.h"
#include "obstructions.h"
#include "fsm.h"
#include "uart.h"
#include "laser.h"
#include "sensors.h"
#include "pwm.h"

#define PCNT_UNIT_MOTOR1 PCNT_UNIT_0
#define PCNT_UNIT_MOTOR2 PCNT_UNIT_1
#define PCNT_UNIT_MOTOR3 PCNT_UNIT_2
#define PCNT_UNIT_MOTOR4 PCNT_UNIT_3
#define STATE_BIT_REVERSE 0
#define STATE_BIT_FWD 1
#define STATE_BIT_HORN 2
#define STATE_BIT_LED 3
#define STATE_CONTROLLER_CONNECTED 4
#define STATE_BIT_R3 5
#define STATE_BIT_CROSS 6
#define STATE_BIT_RECORD 7
#define STATE_BIT_REPLAY 8
#define STATE_BIT_AUTO 9

typedef struct
{
    int unit;
    int motor_revolutions;
    int motor_direction;
} motor_pcnt;

static motor_pcnt motor1_pcnt = {PCNT_UNIT_MOTOR1, 0, 0};
static motor_pcnt motor2_pcnt = {PCNT_UNIT_MOTOR2, 0, 0};
static motor_pcnt motor3_pcnt = {PCNT_UNIT_MOTOR3, 0, 0};
static motor_pcnt motor4_pcnt = {PCNT_UNIT_MOTOR4, 0, 0};

// This is a logarithmic curve generated by motorlogcurve.py
static uint16_t throttle_map_high[] = {0, 2457, 2936, 3276, 3540, 3755, 3938, 4095, 4235, 4359, 4472, 4574, 4669, 4757, 4838, 4914, 4986, 5054, 5117, 5178, 5236, 5291, 5343, 5394, 5442, 5488, 5533, 5576, 5617, 5657, 5696, 5733, 5770, 5805, 5839, 5873, 5905, 5937, 5967, 5997, 6026, 6055, 6083, 6110, 6136, 6162, 6188, 6213, 6237, 6261, 6284, 6307, 6330, 6352, 6373, 6395, 6416, 6436, 6456, 6476, 6496, 6515, 6534, 6553, 6571, 6589, 6607, 6624, 6641, 6658, 6675, 6692, 6708, 6724, 6740, 6756, 6771, 6786, 6801, 6816, 6831, 6845, 6860, 6874, 6888, 6902, 6915, 6929, 6942, 6955, 6968, 6981, 6994, 7007, 7019, 7032, 7044, 7056, 7068, 7080, 7092, 7103, 7115, 7126, 7138, 7149, 7160, 7171, 7182, 7193, 7203, 7214, 7224, 7235, 7245, 7255, 7265, 7275, 7285, 7295, 7305, 7315, 7325, 7334, 7344, 7353, 7362, 7372, 7381, 7390, 7399, 7408, 7417, 7426, 7435, 7443, 7452, 7460, 7469, 7477, 7486, 7494, 7503, 7511, 7519, 7527, 7535, 7543, 7551, 7559, 7567, 7575, 7582, 7590, 7598, 7605, 7613, 7620, 7628, 7635, 7643, 7650, 7657, 7664, 7672, 7679, 7686, 7693, 7700, 7707, 7714, 7721, 7728, 7734, 7741, 7748, 7755, 7761, 7768, 7774, 7781, 7788, 7794, 7800, 7807, 7813, 7820, 7826, 7832, 7838, 7845, 7851, 7857, 7863, 7869, 7875, 7881, 7887, 7893, 7899, 7905, 7911, 7917, 7922, 7928, 7934, 7940, 7945, 7951, 7957, 7962, 7968, 7973, 7979, 7984, 7990, 7995, 8001, 8006, 8012, 8017, 8022, 8028, 8033, 8038, 8043, 8049, 8054, 8059, 8064, 8069, 8074, 8079, 8084, 8090, 8095, 8100, 8105, 8109, 8114, 8119, 8124, 8129, 8134, 8139, 8144, 8148, 8153, 8158, 8163, 8167, 8172, 8177, 8181, 8186, 8191};
// static uint16_t throttle_map_high[] = {0, 1019, 1614, 2037, 2365, 2633, 2860, 3056, 3229, 3384, 3524, 3652, 3769, 3878, 3979, 4074, 4163, 4247, 4327, 4402, 4474, 4542, 4608, 4670, 4730, 4788, 4843, 4897, 4948, 4998, 5046, 5093, 5138, 5182, 5225, 5266, 5306, 5345, 5384, 5421, 5457, 5493, 5527, 5561, 5594, 5626, 5658, 5689, 5719, 5749, 5778, 5806, 5834, 5862, 5889, 5915, 5941, 5967, 5992, 6017, 6041, 6065, 6088, 6111, 6134, 6157, 6179, 6201, 6222, 6243, 6264, 6285, 6305, 6325, 6345, 6364, 6383, 6402, 6421, 6439, 6458, 6476, 6493, 6511, 6528, 6546, 6563, 6579, 6596, 6612, 6629, 6645, 6661, 6676, 6692, 6707, 6723, 6738, 6753, 6767, 6782, 6796, 6811, 6825, 6839, 6853, 6867, 6880, 6894, 6907, 6921, 6934, 6947, 6960, 6973, 6985, 6998, 7011, 7023, 7035, 7047, 7060, 7072, 7083, 7095, 7107, 7119, 7130, 7142, 7153, 7164, 7175, 7186, 7197, 7208, 7219, 7230, 7241, 7251, 7262, 7272, 7283, 7293, 7303, 7313, 7323, 7333, 7343, 7353, 7363, 7373, 7383, 7392, 7402, 7411, 7421, 7430, 7439, 7449, 7458, 7467, 7476, 7485, 7494, 7503, 7512, 7521, 7530, 7538, 7547, 7556, 7564, 7573, 7581, 7590, 7598, 7606, 7615, 7623, 7631, 7639, 7647, 7655, 7663, 7671, 7679, 7687, 7695, 7703, 7711, 7718, 7726, 7734, 7741, 7749, 7756, 7764, 7771, 7779, 7786, 7793, 7801, 7808, 7815, 7822, 7829, 7836, 7844, 7851, 7858, 7865, 7872, 7878, 7885, 7892, 7899, 7906, 7913, 7919, 7926, 7933, 7939, 7946, 7952, 7959, 7965, 7972, 7978, 7985, 7991, 7998, 8004, 8010, 8017, 8023, 8029, 8035, 8042, 8048, 8054, 8060, 8066, 8072, 8078, 8084, 8090, 8096, 8102, 8108, 8114, 8120, 8126, 8131, 8137, 8143, 8191};
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

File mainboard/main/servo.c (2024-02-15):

#include "servo.h"
#include <esp_log.h>

// TODO: Set the right values for each servo, we are now assuming they are all the same
#define SERVO_MIN_PULSEWIDTH_US 500          // Minimum pulse width in microsecond
#define SERVO_MAX_PULSEWIDTH_US 2500         // Maximum pulse width in microsecond
#define SERVO_MIN_DEGREE -90                 // Minimum angle
#define SERVO_MAX_DEGREE 90                  // Maximum angle
#define SERVO_TIMEBASE_RESOLUTION_HZ 1000000 // 1MHz, 1us per tick
#define SERVO_TIMEBASE_PERIOD 20000          // 20000 ticks, 20ms

static const char *TAG = "servo_c";
static mcpwm_timer_handle_t timer0 = NULL;
static mcpwm_timer_handle_t timer1 = NULL;

static inline uint32_t angle_to_compare(int angle)
{
    return (angle - SERVO_MIN_DEGREE) * (SERVO_MAX_PULSEWIDTH_US - SERVO_MIN_PULSEWIDTH_US) / (SERVO_MAX_DEGREE - SERVO_MIN_DEGREE) + SERVO_MIN_PULSEWIDTH_US;
}

static mcpwm_oper_handle_t oper1 = NULL;
static mcpwm_oper_handle_t oper2 = NULL;
static mcpwm_oper_handle_t oper3 = NULL;
static mcpwm_oper_handle_t oper4 = NULL;

static int pwm_count = 0;

void servo_init()
{
    mcpwm_timer_config_t timer_config = {
        .group_id = 0,
        .clk_src = MCPWM_TIMER_CLK_SRC_DEFAULT,
        .resolution_hz = SERVO_TIMEBASE_RESOLUTION_HZ,
        .period_ticks = SERVO_TIMEBASE_PERIOD,
        .count_mode = MCPWM_TIMER_COUNT_MODE_UP,
    };
    ESP_ERROR_CHECK(mcpwm_new_timer(&timer_config, &timer0));

    timer_config.group_id = 1;
    ESP_ERROR_CHECK(mcpwm_new_timer(&timer_config, &timer1));

    mcpwm_operator_config_t operator0_config = {
        .group_id = 0, // operator must be in the same group to the timer
    };
    mcpwm_operator_config_t operator1_config = {
        .group_id = 1, // operator must be in the same group to the timer
    };
    ESP_ERROR_CHECK(mcpwm_new_operator(&operator0_config, &oper1));
    ESP_ERROR_CHECK(mcpwm_new_operator(&operator0_config, &oper2));
    ESP_ERROR_CHECK(mcpwm_new_operator(&operator0_config, &oper3));
    ESP_ERROR_CHECK(mcpwm_new_operator(&operator1_config, &oper4));

    ESP_LOGI(TAG, "Connect timer and operator");
    ESP_ERROR_CHECK(mcpwm_operator_connect_timer(oper1, timer0));
    ESP_ERROR_CHECK(mcpwm_operator_connect_timer(oper2, timer0));
    ESP_ERROR_CHECK(mcpwm_operator_connect_timer(oper3, timer0));
    ESP_ERROR_CHECK(mcpwm_operator_connect_timer(oper4, timer1));
}
void servo_start()
{
    ESP_LOGI(TAG, "Enable and start timer");
    ESP_ERROR_CHECK(mcpwm_timer_enable(timer0));
    ESP_ERROR_CHECK(mcpwm_timer_enable(timer1));
    ESP_ERROR_CHECK(mcpwm_timer_start_stop(timer0, MCPWM_TIMER_START_NO_STOP));
    ESP_ERROR_CHECK(mcpwm_timer_start_stop(timer1, MCPWM_TIMER_START_NO_STOP));
}

void servo_create(uint8_t pin, mcpwm_cmpr_handle_t *comparator)
{
    // We can put 1 PWM pin in 1 comparator. 2 comparator in 1 operator. 3 operator per timers. And we have 2 timers
    static mcpwm_oper_handle_t *oper = NULL;
    if (pwm_count >> 1 == 0)
    {
        oper = &oper1;
    }
    if (pwm_count >> 1 == 1)
    {
        oper = &oper2;
    }
    if (pwm_count >> 1 == 2)
    {
        oper = &oper3;
    }
    if (pwm_count >> 1 == 3)
    {
        oper = &oper4;
    }

    mcpwm_gen_handle_t generator = NULL;
    mcpwm_generator_config_t generator_config = {
        .gen_gpio_num = pin,
    };
    ESP_ERROR_CHECK(mcpwm_new_generator(*oper, &generator_config, &generator));

    ESP_LOGI(TAG, "Create comparator and generator from the operator");
    mcpwm_comparator_config_t comparator_config = {
        .flags.update_cmp_on_tez = true,
    };

    ESP_ERROR_CHECK(mcpwm_new_comparator(*oper, &comparator_config, comparator));

    // set the initial compare value, so that the servo will spin to the center position
    ESP_ERROR_CHECK(mcpwm_comparator_set_compare_value(*comparator, angle_to_compare(0)));

    ESP_LOGI(TAG, "Set generator action on timer and compare event");
    // go high on counter empty
    ESP_ERROR_CHECK(mcpwm_generator_set_action_on_timer_event(generator,
                                                              MCPWM_GEN_TIMER_EVENT_ACTION(MCPWM_TIMER_DIRECTION_UP, MCPWM_TIMER_EVENT_EMPTY, MCPWM_GEN_ACTION_HIGH)));
    // go low on compare threshold
    ESP_ERROR_CHECK(mcpwm_generator_set_action_on_compare_event(generator,
                                                                MCPWM_GEN_COMPARE_EVENT_ACTION(MCPWM_TIMER_DIRECTION_UP, *comparator, MCPWM_GEN_ACTION_LOW)));
    pwm_count++;

    // int angle = 0;
    // ESP_ERROR_CHECK(mcpwm_comparator_set_compare_value(comparator, angle_to_compare(angle)));
}

void servo_enable(mcpwm_cmpr_handle_t *comparator, bool on)
{
    // TODO: turn on or off servo control
    // TODO: keep generators in a list and find them by cpomparator
}

void servo_set_angle(mcpwm_cmpr_handle_t *comparator, int angle)
{
    ESP_ERROR_CHECK(mcpwm_comparator_set_compare_value(*comparator, angle_to_compare(angle)));
}

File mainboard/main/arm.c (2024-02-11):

#include "arm.h"

#include <esp_log.h>
#include "hw_def.h"
#include "string.h"
#include <esp_event.h>
#include "servo.h"
#include "common.h"

#define COMMAND_STOP 1
#define COMMAND_MOVE_ANGLE 2
#define MAX_ANGLE1 55.0  // Base Rotation
#define MIN_ANGLE1 -30.0 // Base Rotation
#define MAX_ANGLE2 54.0  // Boom
#define MIN_ANGLE2 -10.0 // Boom
#define MAX_ANGLE3 30.0  // Grapple
#define MIN_ANGLE3 -35.0 // Grapple
#define MAX_ANGLE4 25.0  // Arm
#define MIN_ANGLE4 -90.0 // Arm

typedef struct
{
    uint8_t command;
    int8_t angle_velocity_lx;
    int8_t angle_velocity_ly;
    int8_t angle_velocity_rx;
    int8_t angle_velocity_ry;
} q_msg;

static QueueHandle_t xQueue;
static const char *TAG = "arm_c";
static bool status_arm_enabled = false;
static mcpwm_cmpr_handle_t arm_boom_rotator;
static mcpwm_cmpr_handle_t arm_boom;
static mcpwm_cmpr_handle_t arm_arm;
static mcpwm_cmpr_handle_t arm_grapple;

extern metrics_t metrics;

void arm_move(int8_t lx, int8_t ly, int8_t rx, int8_t ry)
{
    if (!status_arm_enabled)
    {
        return;
    }

    lx = lx / 2;
    ly = ly / 2;
    rx = rx / 2;
    ry = ry / 2;

    if ((lx > 4 || lx < -4) || (ly > 4 || ly < -4) || (rx > 4 || rx < -4) || (ry > 4 || ry < -4))
    {
        q_msg msg;
        msg.command = COMMAND_MOVE_ANGLE;
        msg.angle_velocity_lx = lx;
        msg.angle_velocity_ly = ly;
        msg.angle_velocity_rx = rx;
        msg.angle_velocity_ry = ry;
        xQueueSend(xQueue, (void *)&msg, 0);
    }
    else
    {
        // TODO: if already stopped, dont stop again or we will wakeup the task for nothing
        q_msg msg;
        msg.command = COMMAND_STOP;
        xQueueSend(xQueue, (void *)&msg, 0);
    }
}

void arm_enable(bool enabled)
{
    if (status_arm_enabled == enabled)
    {
        return;
    }

    status_arm_enabled = enabled;
    if (!status_arm_enabled)
    {
        q_msg msg;
        msg.command = COMMAND_STOP;
        xQueueSend(xQueue, (void *)&msg, 0);
    }
}

void arm_task(void *arg)
{

    q_msg msg;
    float angle1 = 0;
    float angle2 = MIN_ANGLE2;
    float angle3 = MIN_ANGLE3;
    float angle4 = MIN_ANGLE4;

    while (1)
    {
        ESP_LOGI(TAG, "Checking for ARM queue msg");
        if (xQueueReceive(xQueue, &msg, 60000))
        {
            ESP_LOGI(TAG, "ARM queue msg received");
            if (msg.command == COMMAND_STOP)
            {
                // Stop all. Don't do anything. Just go back to waiting for a message
            }
            else if (msg.command == COMMAND_MOVE_ANGLE)
            {
/*
Axis values range from -63 to 63
angles range from -90 to 90
an axis value 0f 63 will ramp up the angle from 0 to 63 within 1s
    so a speed of 6.3 per 100ms
*/
#define RESOLUTION 20
                float delta1 = (float)(0 - msg.angle_velocity_lx) / RESOLUTION;
                float delta2 = (float)msg.angle_velocity_ly / RESOLUTION;
                float delta3 = (float)msg.angle_velocity_rx / RESOLUTION;
                float delta4 = (float)(msg.angle_velocity_ry) / RESOLUTION; // reverse sign since motor is installed the other way around

                // always just take the highest delta for one stick. This is to avoid controlling 2 servos on the same stick
                if (abs(delta1) > abs(delta2))
                {
                    delta2 = 0;
                }
                else
                {
                    delta1 = 0;
                }
                if (abs(delta3) > abs(delta4))
                {
                    delta4 = 0;
                }
                else
                {
                    delta3 = 0;
                }

                while (!uxQueueMessagesWaiting(xQueue))
                {
                    angle1 += delta1;
                    angle2 += delta2;
                    angle3 += delta3;
                    angle4 += delta4;

                    if (angle1 > MAX_ANGLE1)
                    {
                        angle1 = MAX_ANGLE1;
                    }
                    if (angle2 > MAX_ANGLE2)
                    {
                        angle2 = MAX_ANGLE2;
                    }
                    if (angle3 > MAX_ANGLE3)
                    {
                        angle3 = MAX_ANGLE3;
                    }
                    if (angle4 > MAX_ANGLE4)
                    {
                        angle4 = MAX_ANGLE4;
                    }
                    if (angle1 < MIN_ANGLE1)
                    {
                        angle1 = MIN_ANGLE1;
                    }
                    if (angle2 < MIN_ANGLE2)
                    {
                        angle2 = MIN_ANGLE2;
                    }
                    if (angle3 < MIN_ANGLE3)
                    {
                        angle3 = MIN_ANGLE3;
                    }
                    if (angle4 < MIN_ANGLE4)
                    {
                        angle4 = MIN_ANGLE4;
                    }

                    metrics.angle_rotator = angle1;
                    metrics.angle_boom = angle2;
                    metrics.angle_grapple = angle3;
                    metrics.angle_arm = angle4;
                    servo_set_angle(&arm_boom_rotator, angle1);
                    servo_set_angle(&arm_boom, angle2);
                    servo_set_angle(&arm_grapple, angle3);
                    servo_set_angle(&arm_arm, angle4);

                    vTaskDelay((1000 / RESOLUTION) / portTICK_PERIOD_MS);
                }
            }
        }
    }
}

void arm_init()
{
    xQueue = xQueueCreate(4, sizeof(q_msg));

    servo_create(GPIO_ARM_SERVO1, &arm_boom_rotator);
    servo_create(GPIO_ARM_SERVO2, &arm_boom);
    servo_create(GPIO_ARM_SERVO3, &arm_grapple);
    servo_create(GPIO_ARM_SERVO4, &arm_arm);

    servo_set_angle(&arm_boom_rotator, 0);
    servo_set_angle(&arm_boom, MIN_ANGLE2);
    servo_set_angle(&arm_arm, MIN_ANGLE4);
    servo_set_angle(&arm_grapple, MIN_ANGLE3);

    xTaskCreate(arm_task, "arm_task", 4096, NULL, 5, NULL);
}

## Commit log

2024-01-24 first
    update
    readme
    [design.fzz, partitions.csv]
2024-01-28 arm code
2024-02-02 Dualsense works with extended reports and can control rumble and LEDs
2024-02-06 Changed i2c to uart
2024-02-15 Collision detection
    [bumper-rear.FCStd, bumper.FCStd, untitled.brd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]
2024-03-02 battery voltage monitor
2024-03-03 changed buzzer to use ledc
    [buzzer.c, hardware.c, obstructions.c]

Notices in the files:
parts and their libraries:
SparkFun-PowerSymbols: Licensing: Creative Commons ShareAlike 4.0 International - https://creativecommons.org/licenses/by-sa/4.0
